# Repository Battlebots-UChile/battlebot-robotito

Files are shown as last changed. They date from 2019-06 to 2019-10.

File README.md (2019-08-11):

# Robotito
Robotito fue realizado en el taller de proyecto "Contruye tu battlebot", el cuál combina conocimientos de electrónica, mecánica y programación, bajo un acorazado de metal giratorio.
<center><center>

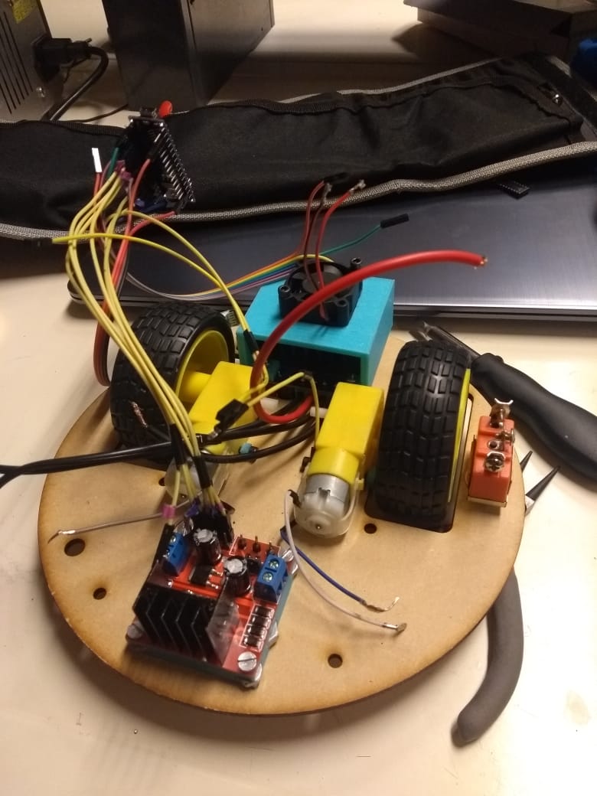
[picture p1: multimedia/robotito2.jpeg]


## Integrantes
- Leslie Cárdenas - FCFM
- Tomás Ceballos - FCFM
- Francisca Guiñez - FCFM
- Keyla Sandoval - FCFM

## Descripción del proyecto

Robotito es un robot, pero no cualquier tipo de robot, NOOO... es un BATTLEBOT (por si no quedo claro en los títulos), controlado mediante una aplicación celular (App-Inventor), cuyo objetivo en la vida es detener todos los golpes que intenten destruirlo.

Funciona en base a dos motores DC básicos, uno conectado a cada rueda, y un motor DC de 2500 rpm conectado a un bowl de cocina, a través de una pieza impresa en 3D. Cuenta con dos puentes H, uno dual y uno single, y es alimentado por dos baterias LiPo.

### Descripción morfológica
La forma elegida para nuestro robot surgió de pensar en cual sería la más óptima defensiva. Por esto nos inclinamos por utilizar un bowl. Pensamos que, por un lado, su forma semiesférica iba a imposibilitar cualquier intento de agarrarlo.
Además, al estar hecho de acero inoxidable claramente iba a ser poco probable que le produjeran daños graves.

Cabe decir que antes de tomar una decisión realizamos una exhaustiva investigación en Youtube sobre battlebots alrededor del mundo

### Estrategia utilizada

La mejor estrategia para ganar con Robotito es:
- Evitando ataques laterales: Creemos que lo que podría dañar el bowl serían golpes muy reiterativos, contundentes y punzantes de alguna forma. Por ejemplo una barra o punta de un material lo suficientemente resistente. Por lo que lo ideal es evitarlos.
- Interponiendosea a la trayetoria del arma del robocontrincante: Como Robotito es un bowl de metal, en general los golpes no lo afectan. La idea es entonces que el motor que controla el arma del contrincante sea sometido a pick de corriente que lo imposibiliten de seguir golpeandolo por un tiempo. Esto para dar opcion al siguiente punto.
- Alejarse del oponente cuando sea posible: Esto es mas que todo para evitar golpes innecesarios que no vayan a ayudar en la estrategia anteriormente mencionada. Es una buena idea alejarse, luego posicionarse y direccionarse hacia el roboenemigo en busca de un empujón que lo lleve al borde la pista, o bien, hacia alguna arma que pueda haber en esta.  
Una demostración de esto se puede ver [aquí](https://drive.google.com/file/d/1hvNaAUOcBa2c_J4brZBd_sA4WgRW3LiS/view?usp=sharing).

#### Datos defensivos
El bowl es nuestra principal , pero no única, defensa. Es de acero inoxidable. Proviene directamente de la cocina de una de las integrantes de nuestro grupo :).  
Pero como un pedazo de metal no puede con todo (¿o si?), para detener los posibles ataques a ras de suelo (ya que el bowl deja un par de centímetros al descubierto), nuestro battlebot cuenta con lo que denominamos una "falda", cortada con laser en MDF de 6mm.
Además, cabe decir que la forma circular o semiesférica conseguida también ayuda a que los golpes no lleguen de forma directa.

### Descripción control
Robotito tiene su propia app para Android, la cual pueden descargar [aquí](https://github.com/Battlebots-UChile/battlebot-robotito/tree/master/codigos/APK).
Al ingresar, se pueden ver 3 secciones:

#### Conexión
Para conectar la app al módulo BT del robot, basta con:
1. Prender el robot (nunca está de más cerciorarse)
2. Activar el Bluetooth del celular
3. Entrar a la app desde el celular
4. Presionar "Buscar dispositivos"
5. Seleccionar el nombre correspondiente al módulo bluetooth (modificable, Google es la luz)
6. Esperar. Cuando la luz del módulo BT deje de parpadear, será un indicador de que se ha establecido una conexión.

#### Movimiento
Estos 7 botones cumplen con el objetivo de movilizar nuestro robot. Cuando se presiona un botón, la orden se manda de manera constante, es decir, que, a menos que se presione otro, la acción se seguirá ejecutando.  
A continuación, se especifica cómo giran los motores, dependiendo del botón presionado. 
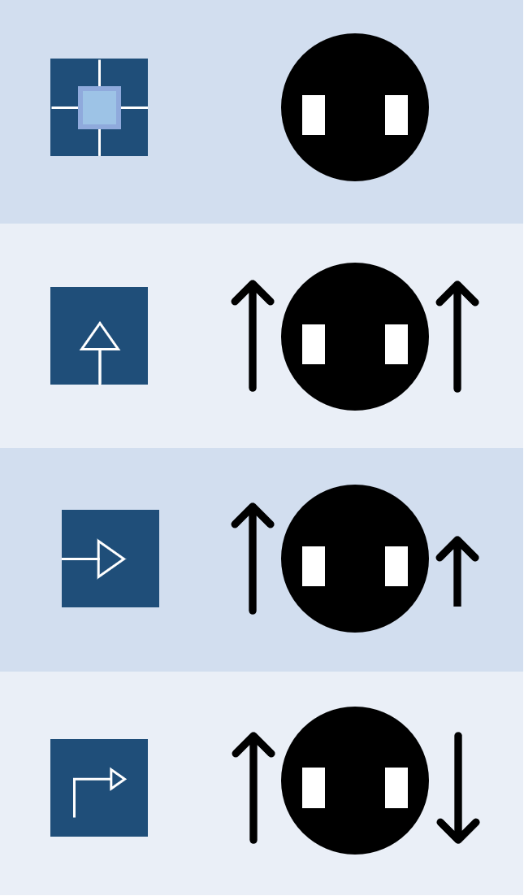
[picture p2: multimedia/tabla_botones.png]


#### Arma y emergencia
En caso de emergencia de debe presionar el botón STOP. ¿Qué hace? Manda una señal que detiene el movimiento de los 3 motores que componen a Robotito de manera instantánea (en cuando la señal sea recibida). No afecta el funcionamiento del ventilador, ya que funciona de manera independiente.
Luego, podemos ver una numeración de 5 botones, los cuales son las posibles velocidades del arma (se pueden modificar dentro del código. ino, pero no lo sugerimos). En "0" el motor no se mueve. Si se presiona cualquiera que modifique la velocidad actual, el aumento o descenso será paulatino.
#### Otros
La app también cuenta con un particular sonido al presionar algunas de las teclas. Fuente: desconocida.  
Además, cuenta con la posibilidad de activar la reproducción de la canción "Mr. Roboto", presionando el switch de la parte inferior.

##  Paso a Paso

### Materiales:
- 1 Arduino Nano
- 1 Bowl de acero inoxidable
- 1 Rueda loca
- 2 Motores DC con ruedas
- 1 Puente H BTS7960
- 1 Puente H dual L298n
- 1 Módulo Bluetooth HC-06
- 2 Baterías Li-Po de 7.4V
- 1 Ventilador de 30x30mm
- 3 Ruedas de 20mm
- 4 Separadores hexagonales de 50mm (\*)
- 20 cm de Velcro
- 2 Conectores hembra HT60 (\*\*)
- 2 Interruptores (\*\*\*)
- 4 Pernos de 2mm
- 2 Tuercas de 2mm
- Pernos y tuercas de 3mm
- Cables
- Cables para Arduino
- Placa MDF de 3mm (opcional 6mm)
- Soldadura para electrónica
- Termoretráctil de varias medidas
- Adhesivo instantáneo, como La Gotita (\*\*\*\*)
- Pines hembra

### Herramientas:
- Alicates varios
- Destornilladores varios
- Pistola de calor o encendedor
- Cautín
- Dremel
- Impresora 3D
- Cortadora Láser
- Limas metálicas
- Pistola de silicona c/repuestos
- Celular Android

### Opcionales:
- Alarma para Li-Po
- Cargador de Li-Po

(\*) o alguna combinación que resulte en esa altura.  
(\*\*) o del tipo que corresponda, según el conector de las LiPos.  
(\*\*\*) Debe poder soportar la corriente del motor. Nosotros usamos uno que soportaba 15A.  
(\*\*\*\*) No nos auspician :(
### Instrucciones

1. Imprimir las piezas en 3d, desde [aquí](https://github.com/Battlebots-UChile/battlebot-robotito/tree/master/planos/Piezas%203d), según lo que se indica en su descripción, y lijar para eliminar imperfecciones.  
2. Cortar las dos bases para el robot, desde [aquí](https://github.com/Battlebots-UChile/battlebot-robotito/tree/master/planos/Bases) y quitar imperfecciones.
3. Conectar el Arduino Nano a un PC, y cargar el [codigo](https://github.com/Battlebots-UChile/battlebot-robotito/tree/master/codigos/arduino/app_bt).
4. Descargar el [apk](https://github.com/Battlebots-UChile/battlebot-robotito/tree/master/codigos/APK) mediante el celular y ejecutar el instalador.
5. Probar las componentes individualmente.
6. Ubicar los [motores DC](https://www.wiltronics.com.au/wp-content/uploads/images/make-and-create/gear-motor-dc-toy-car-wheel-arduino.jpg) con sus respectivas ruedas, utilizando el [agarre 1](https://github.com/Battlebots-UChile/battlebot-robotito/blob/master/planos/Piezas%203d/agarre_yellowmotor1.stl) y el [agarre 2](https://github.com/Battlebots-UChile/battlebot-robotito/blob/master/planos/Piezas%203d/agarre_yellowmotor2.stl) en la base cortada con láser que tiene los orificios para las ruedas, utilizando 4 pernos de 3mm. Esta parte puede ser un poco complicada, pero de ser necesario las piezas 3d se pueden lijar un poco más.   
Para reforzar, aplicar el adhesivo instantáneo a la unión entre las piezas 3d y la base. 
7. Solo con pernos(3mm) (con 2 es suficiente), agarrar el ventilador a la [base del ventilador](https://github.com/Battlebots-UChile/battlebot-robotito/blob/master/planos/Piezas%203d/base_ventilador.stl) y posteriormente al puente H BTS7960. Esto último, solo con 2 orificios opuestos utilizando pernos de 2 mm (la tuerca va puesta por el lado de la pieza 3d).
8. A la estructura anterior, agregarle la [base](https://github.com/Battlebots-UChile/battlebot-robotito/blob/master/planos/Piezas%203d/base_bts7960.stl), utilizando pernos de 3 mm, y ensamblar a la base de las ruedas en la posición determinada. En este punto se puede notar que los pines del puente H quedan hacia la base. Nosotros creamos una pequeña pieza, que no ha sido detallada, debido a que tuvo fallas y será definitivamente modificada.
9. Juntar el puente H L298n a su respectiva [base](https://github.com/Battlebots-UChile/battlebot-robotito/blob/master/planos/Piezas%203d/base_l298n.stl). Para esto, primero se deben ubicar las tuercas en los orificios que correspondan. Luego, con pernos de un largo limitado (posiblemente deban cortarlos), agarrar el puente H.
10. Ensamblar como se detalla en el [esquema](https://github.com/Battlebots-UChile/battlebot-robotito/blob/master/multimedia/esquema_rueda.png), agregando pernos donde corresponda.
11. Cortar dos pedazos de velcro, del tamaño de las baterías y, con silicona caliente (y mucho cuidado, nunca se sabe), pegárselos.
12. Para fijar el Arduino a la base de arriba, también se hizo una pieza, que se evidencia en la siguiente imagen. (algún día estará acá)
13. Agregar los interruptores en los orificios laterales a las ruedas.
14. Usar [esto](https://github.com/Battlebots-UChile/battlebot-robotito/blob/master/planos/Piezas%203d/agarre_motorarma.stl) para fijar el motor del arma a la base de arriba. Primero introducir con mucho cuidado los pernos que agarran el motor con la pieza 3d.
15. Teniendo en cuenta las [conexiones](https://github.com/Battlebots-UChile/battlebot-robotito/tree/master/diagrama), ahora se puede comenzar a cablear.  
Tener en cuenta: no mantener conectadas las baterías cuando se realice esto. Tener claro cuando los interruptores no están dejando pasar energía. Todas los GND deben estar conectados. La base de arriba tiene orificios para los conectores HT60 de las baterías. Para las conexiones desde la LiPo al puente H BTS7960 se debe utilizar un cable más grueso que pueda soportar altos de corriente.
16. Probar las direcciones de las ruedas, si estas no tienen sentido, probar rotar cables de los motores de las ruedas.
17. Si existe algún otro problema operacional, consultar sección [Problema-Solución](https://github.com/Battlebots-UChile/battlebot-robotito#problema---solución)
18. Una vez que todos los motores funcionen según las indicaciones dadas por la app, se recomienda fijar los cables de Arduino con silicona caliente, o en el caso de ser necesario, soldar.
19. Agregar los separadores en los espacios determinados con pernos y tuercas.
20. Al bowl realizarle 3 orificios con un taladro a 40mm desde el centro, ser lo más preciso posible. Esto puede ser muy complicado, por lo que: paciencia.
21. Fijar la [pieza](https://github.com/Battlebots-UChile/battlebot-robotito/blob/master/planos/Piezas%203d/agarre_motorbowl.stl) al bowl, usando pernos.
22. Posicionar la pieza anterior sobre el motor del arma.
23. Destruir a todos

## Problema - Solución
1. Conexiones sueltas  	
Inicialmente teníamos muchas conexiones que estaban agarradas mediante cinta aislante. Pero llegó un punto en el desarrollo del robot donde esto no era eficiente, ya que, debido a la gran cantidad de cables y componentes, estas se soltaban regularmente y entorpecía el avance.  
Solución: Aprender a soldar. Soldar todo lo que estaba más o menos fijo (referido a: Si, este cable va con este hasta el fin de los tiempos) y obviamente funcional.

2. No se cargaba el código al Arduino  
El principal error cuando uno se inicia en el uso de Arduino y módulos BT, es conectar los pines RX y TX con sus opuestos en el otro dispositivo. En el Arduino estos están designados a los pines 0 y 1, pero cuando están ocupados: no se le puede cargar otro código, ni tampoco interactuar con el Serial.  
Solución: Designar nuevos pines RX y TX dentro del Arduino, con la librería SofwareSerial. 

3. El motor del arma no giraba de manera constante  
Desde un principio, la corriente del motor del arma fue desconocida, por lo que, al momento de conectarlo a diversas pilas y baterías, no alcanza la velocidad ni la fuerza que buscábamos.  
Solución: Utilizar baterías LiPo. Su principal característica es que puede entregar mucha corriente en poco tiempo, justo lo que necesitábamos.

4. Quemamos un puente H  
La gran cantidad de amperaje quemo nuestro puente H inicial (VNH2SP30), ya que los 30A que supusimos podía soportar eran solo para picks, no de manera continua. Por esto, se calentaba hasta los 70-100°C.  
Solución: Lo reemplazamos por el BTS7960, capaz de soportar 40A de manera continua. Este cuenta un disipador bastante grande y un ventilador.

5. Cables rozando con el bowl  
Provocaba que el motor del arma necesitara más corriente para funcionar y ocasionaba que las baterías se gastaran más rapido.  
Solución: Tomar los cables del piso superior con una pieza plástica y pegar otros con silicona caliente.

6. Falta de espacio  
Al decidirnos a utilizar un bowl, creímos que el espacio no iba a ser un problema, pero con el cambio de baterías, nos faltaba.  
Solución: Cambiar un Arduino Uno por un Arduino Nano. Reubicar componentes.

### Proyecciones a futuro
* Cambiar el método de control: es decir, en vez de usar la App, crearemos un control con botones y un joystick. Esto ya está en proceso y sus respectivos códigos están actualizados y funcionales.
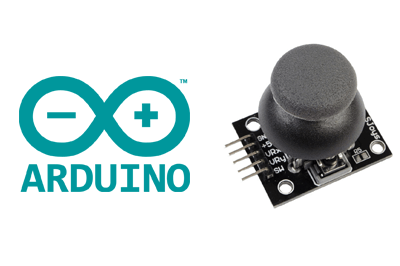
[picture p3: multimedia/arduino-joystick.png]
Joystick con Arduino
#### 
* Adición de un arma: Fijaremos a la parte inferior del bowl una estructura hecha de placa MDF, la cual constará de un anillo con tres protuberancias. La idea es que debido a la velocidad y la fuerza con la que gira el bowl, si un roboenemigo se acerca lo suficiente, este sera levantado y dejado caer en reiteradas ocasiones en un periodo corto de tiempo, con la intención de provocar sacudidas que puedan dañar interna y/o externamente a los demás robots. (Planos: Próximamente...)

## Licencia
<br />Esta obra está bajo una <a rel="license" href="http://creativecommons.org/licenses/by-nc/4.0/">Licencia Creative Commons Atribución-NoComercial 4.0 Internacional</a>.

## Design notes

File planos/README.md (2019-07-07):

# Archivos de planos incluidos

 En esta carpeta se encuentran todos los planos pra la cortadora laser o la impresora 3D, las dos sub-carpetas son:

 - Bases: en ella  esta contenida la estrucutura interna del battlebot construida con placa MDF de 6mm en una cortadora láser
 - Piezas 3D: Aquí estan todas las estructuras hechas en impresora 3D , las cuales son principalmente de agarre a la estrucutura principal del battlebot y al bool

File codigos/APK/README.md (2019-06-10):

# Código de la Aplicación
Este aplicacion fue usada en la primera version de Robotito.

Cuenta con botones para controlar la velocidad del arma principal y la dirección del robot.

Subir archivo **.apk** y código de la APK ([descargar desde acá](http://appinventor.mit.edu/explore/support/sharing-code.html))

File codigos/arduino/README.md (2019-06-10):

# Códigos Arduino

Robotito_bluetooth cuanta con el código necesario para controlar al robot, mediante la app.

(En proceso) 
Robotito_joystick cuenta con los códigos necesarios para controlar al robot, mediante el Control.
control.ino va cargado al arduino del control
robot.ino va cargado al arduino del robot

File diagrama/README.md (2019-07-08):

# Diagrama electromecánico
 Aquí se encuentran los digramas eléctricos de robotito en tres formatos, dos visuales y uno en extension fzz.
 Los archivos con extensión jpg muestran todos los componentes y sus conexiones siendo uno hecho en fritzing por lo que el lenguaje y simbología del mismo es un poco más compleja y profesional; el otro archivo es de thinkercad por lo que visualemte es más comprensible, es recomendado empezar por este.

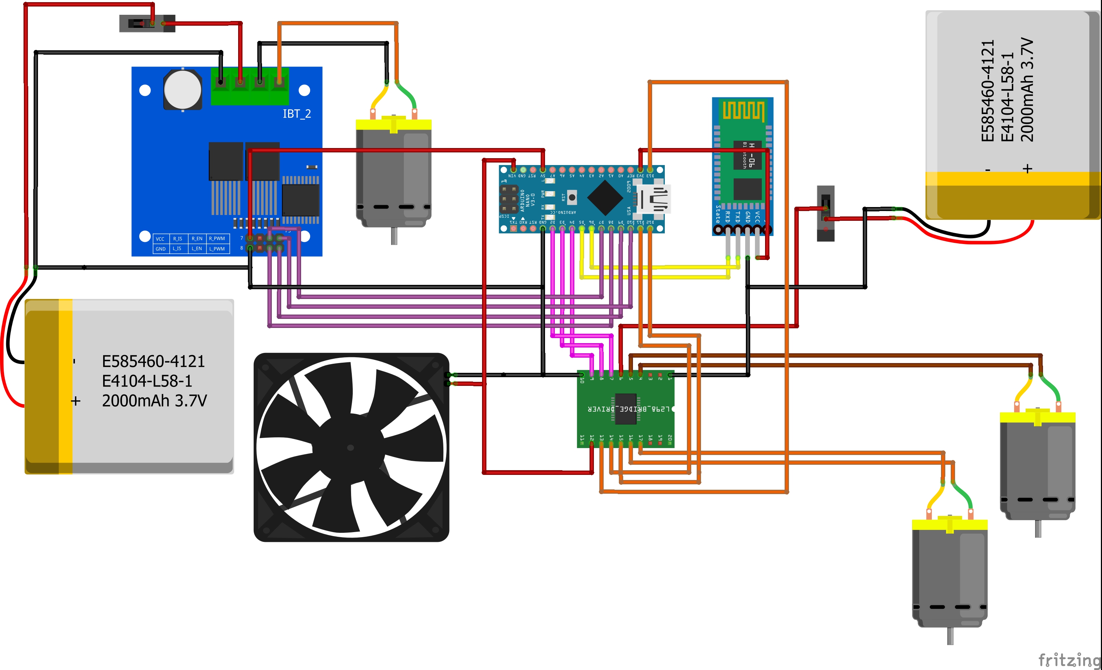
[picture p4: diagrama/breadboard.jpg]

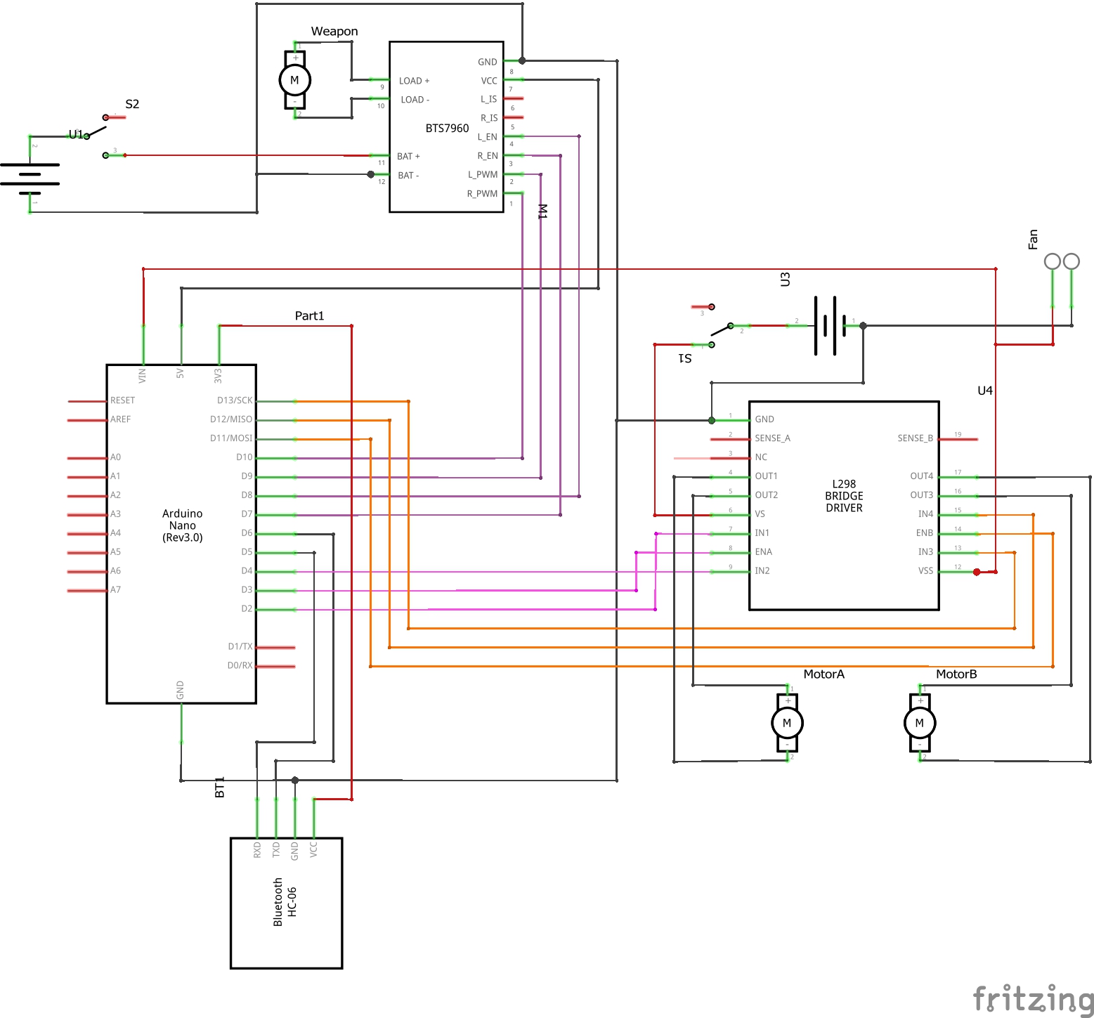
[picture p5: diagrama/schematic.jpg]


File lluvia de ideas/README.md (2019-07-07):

# Lluvia de Ideas
Iniciamos nuestro proyecto solo con dos opciones :Una constaba de un carro convencional con la  particuliaridad de una plataforma movible cuya función era ubicarse bajo los otros robots y mediante un mecanismo levantarlos volcándolos lo que nos haría ganar la batalla. El segundo modelo  (que fue el elegido) era una especie de platillo volador (inspirado en el mismo concepto) con ruedas pero que podía girar sobre si mismo.
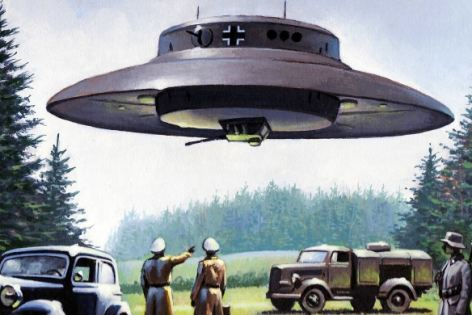
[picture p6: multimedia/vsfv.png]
Modelo 2(OVNI)
#### 

Las armas eran variadas pero se centraba en:Un paralelepípedo giratorio con puntas en los bordes acoplado en el “techo” del OVNI o carro.
Una bola metálica acoplada a una varilla giratoria pegada en el techo del OVNI o carro(todavía no se sabía si era una cuerda o directamente una varilla rigida)
#### Bosquejos con armas integradas
En esta imagen se ven ambos prototipos con las armas anteriormente mencionadas en especial con la bola de demolición.El primero es el OVNI con la bola e inclusive en su momento barajamos la opcion de poner mas de una que solo se movieran con el casco; el segundo bosquejo es el carro tambien con la bola.

Estas dos vías entre battlebots respondían a dos necesidades, proteccion y ataque; la opción de la plataforma brindaba una especie de "falda" que evitaria que otros robots se metieran por debajo con sus armas y nos volcaran o sacaran nuestra tripas. El segundo modelo dada a la velocidad del giro evitaría que fuesemos golpeados directamente y en realidad ver este modelo en acción a travéz de battlebot GIGABYTE  en la pelea  (https://www.youtube.com/watch?v=hSRnhd6K6kY) nos convencio para seguir ese camino.
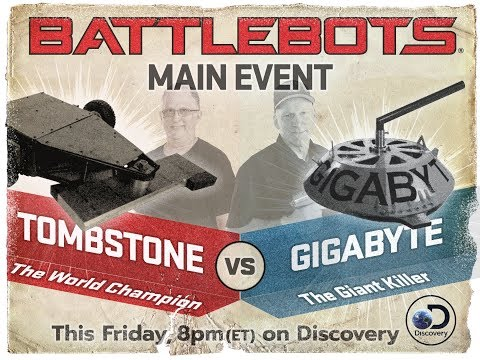
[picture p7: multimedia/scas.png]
Pariente de robotito
####

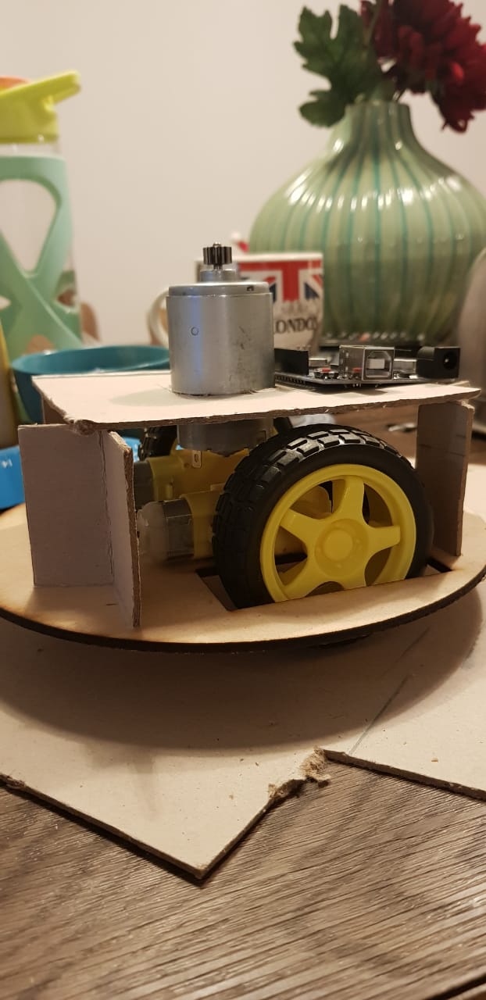
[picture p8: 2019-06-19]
multimedia/cuerpo.jpeg

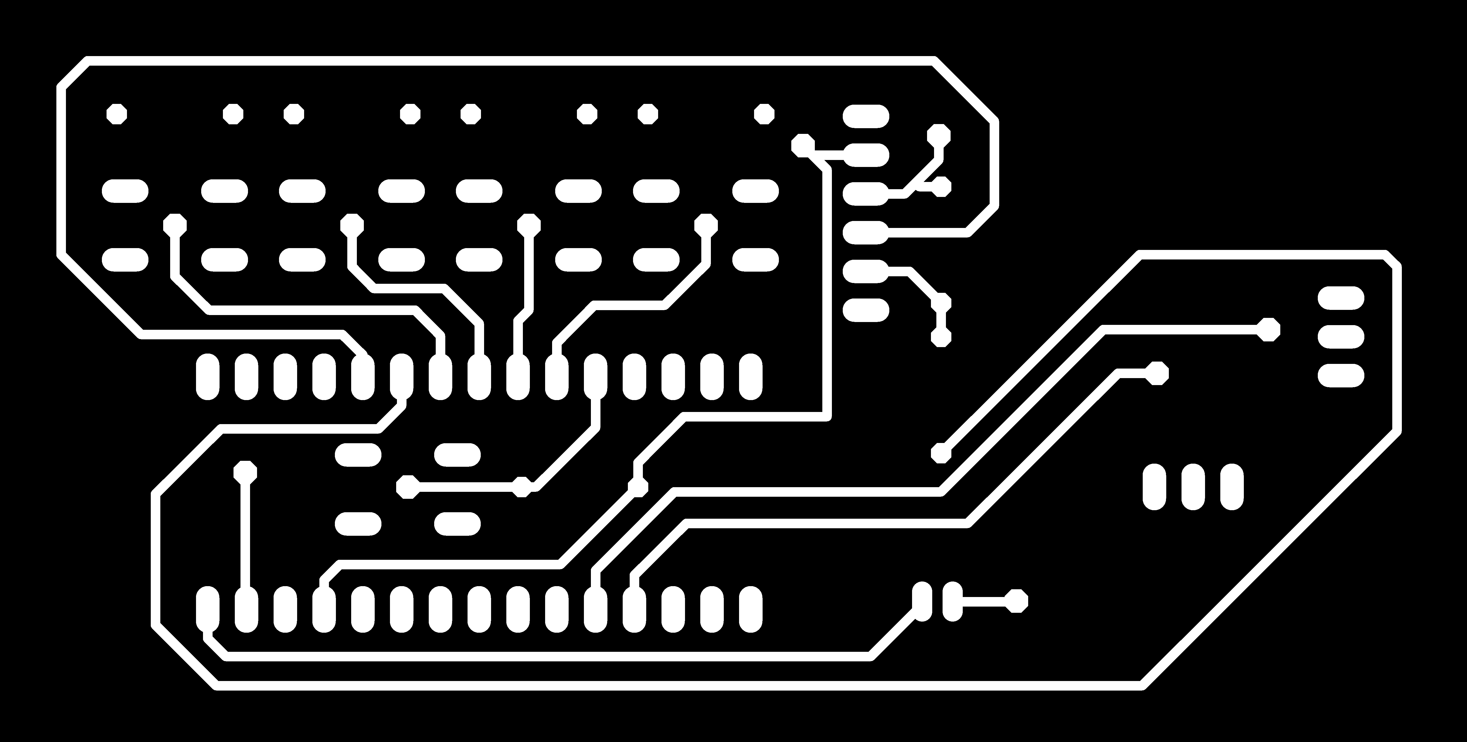
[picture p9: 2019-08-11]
planos/PCB/top.png

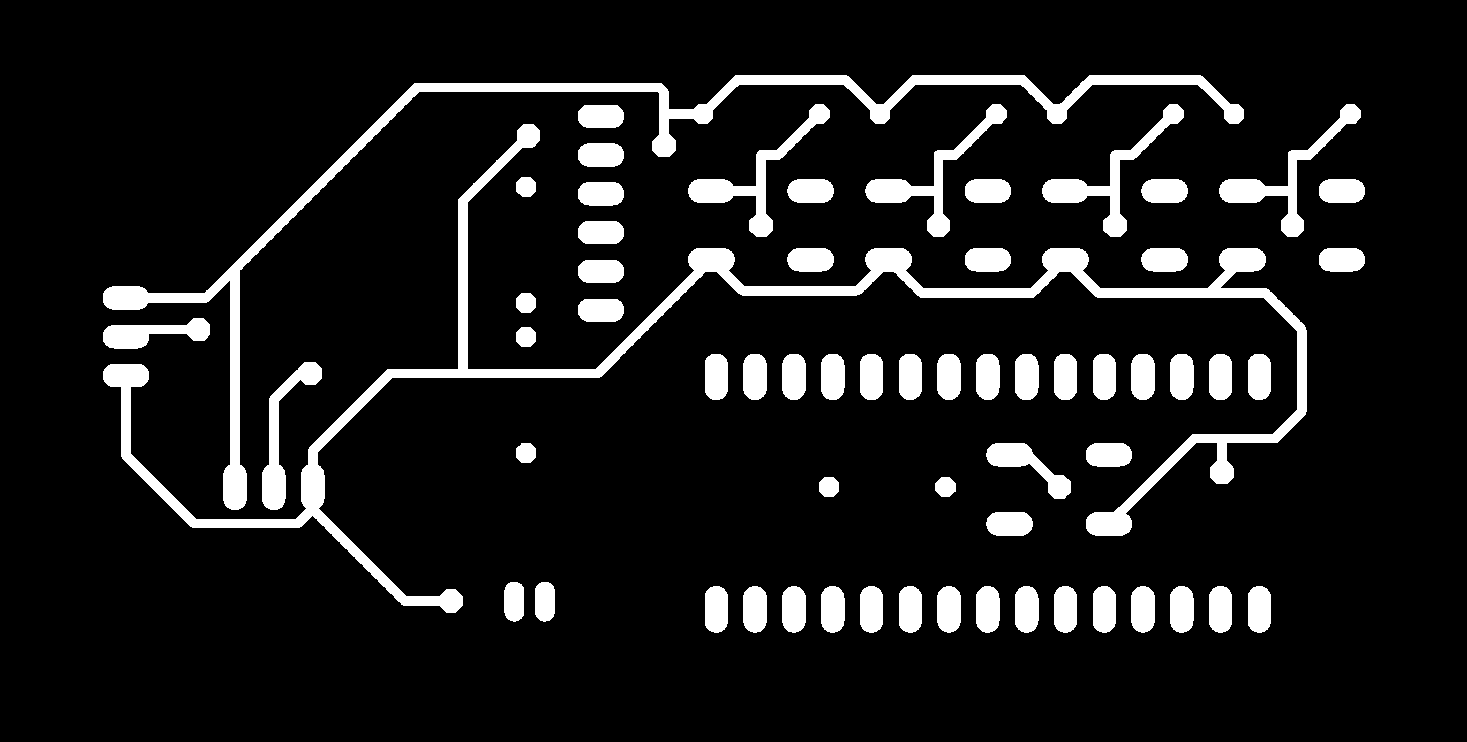
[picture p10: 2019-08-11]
planos/PCB/bottom.png

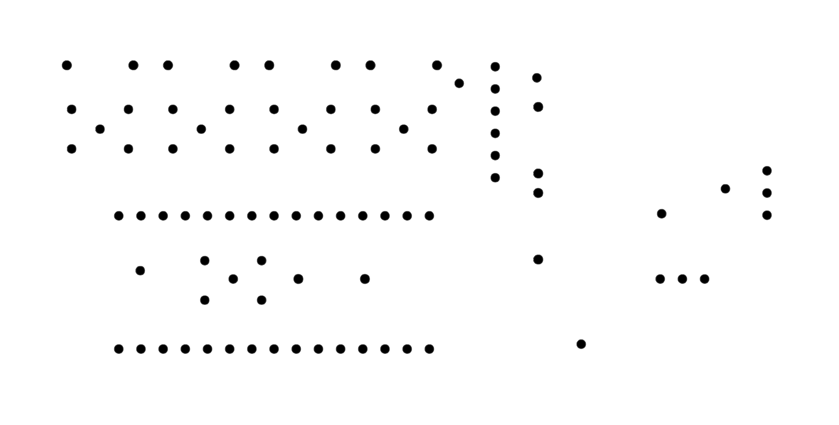
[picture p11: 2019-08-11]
planos/PCB/drills.png

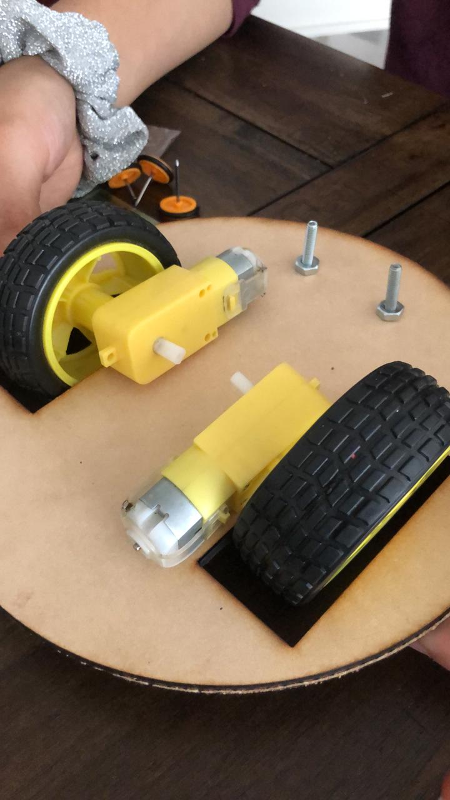
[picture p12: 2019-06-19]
multimedia/ruedas.jpeg

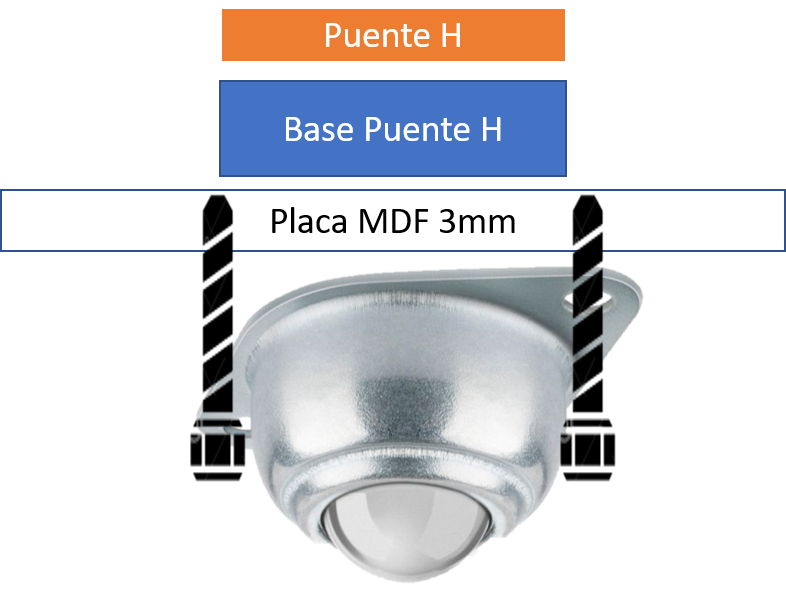
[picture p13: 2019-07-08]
multimedia/esquema_rueda.png

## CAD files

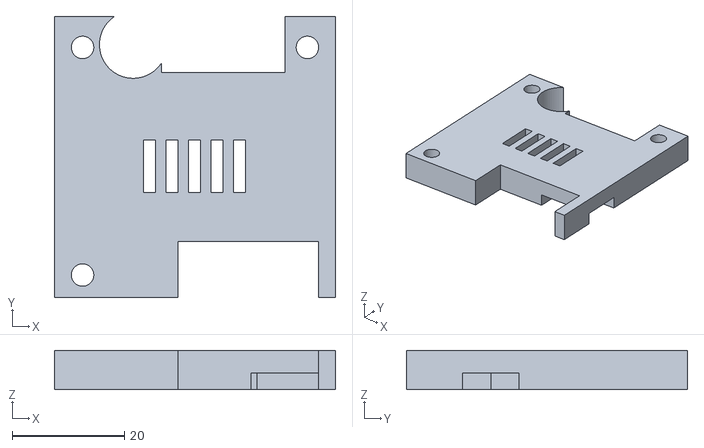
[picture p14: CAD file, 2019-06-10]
planos/Piezas 3d/base_bts7960.stl
50.0 x 50.0 x 7.00

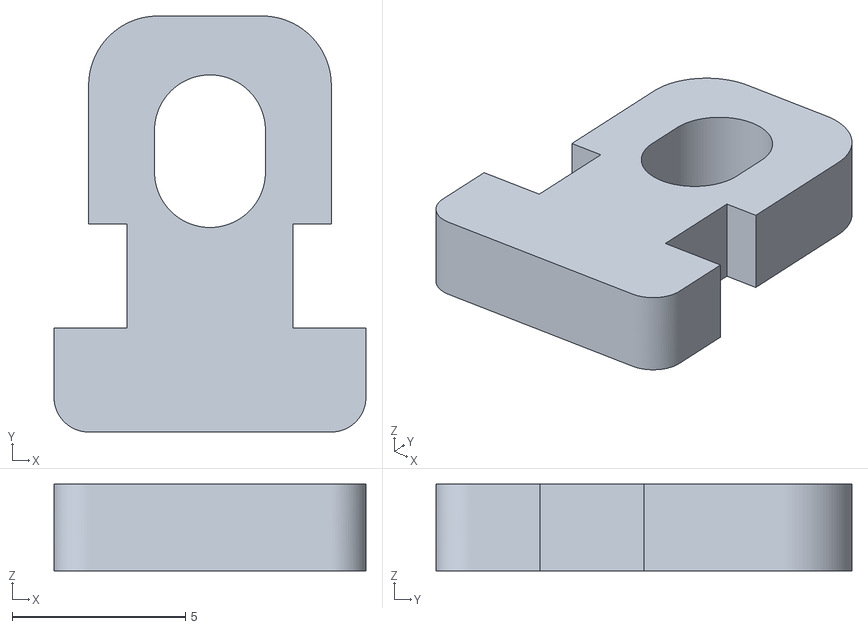
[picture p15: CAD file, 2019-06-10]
planos/Piezas 3d/agarre_yellowmotor1.stl
9.00 x 12.0 x 2.50

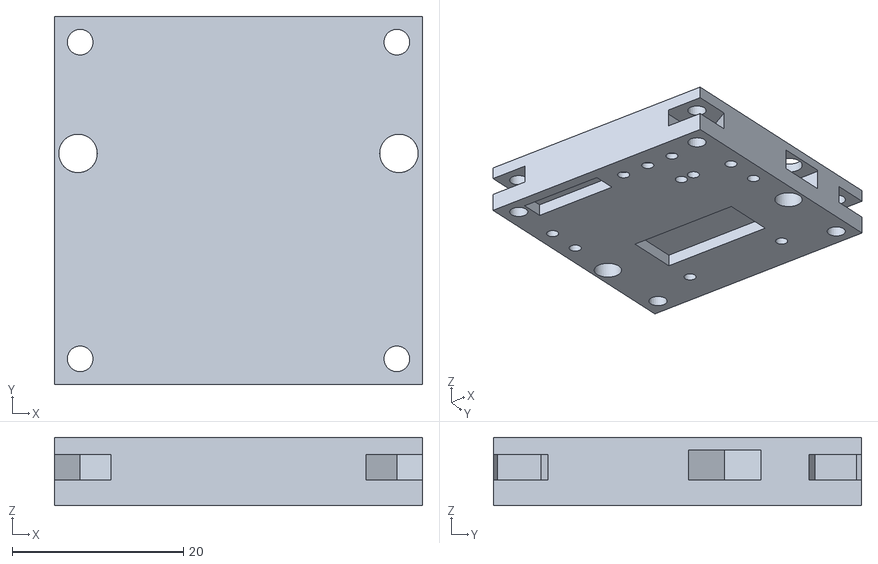
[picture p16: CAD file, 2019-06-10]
planos/Piezas 3d/base_l298n.stl
43.0 x 43.0 x 8.00

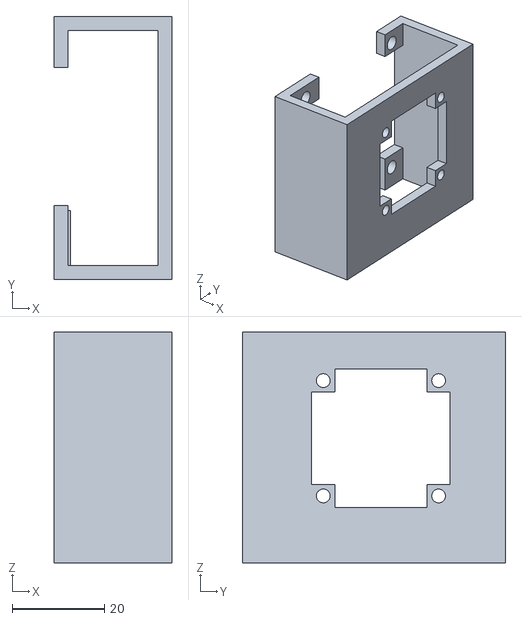
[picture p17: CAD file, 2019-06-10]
planos/Piezas 3d/base_ventilador.stl
25.5 x 57.0 x 50.0

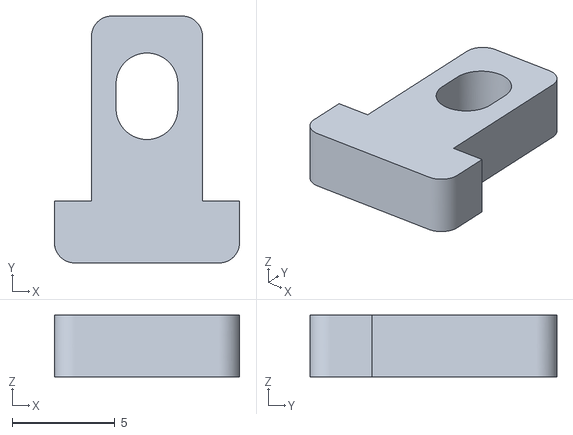
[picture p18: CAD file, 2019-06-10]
planos/Piezas 3d/agarre_yellowmotor2.stl
9.00 x 12.0 x 3.00

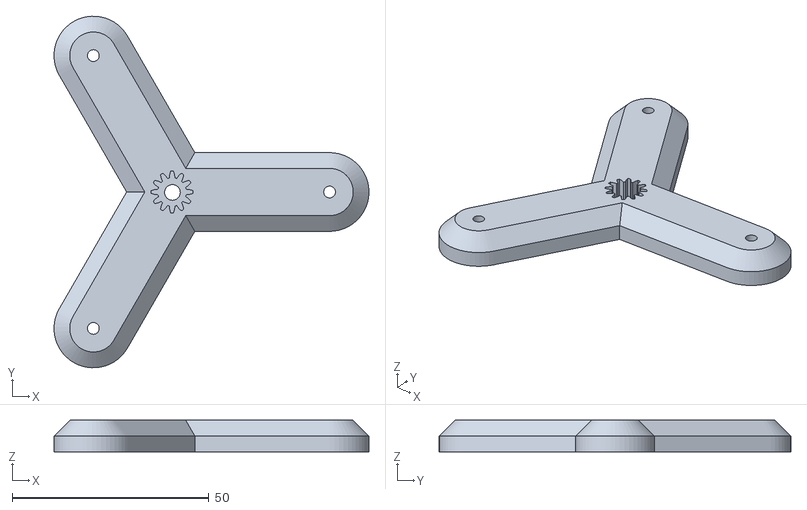
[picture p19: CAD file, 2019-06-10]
planos/Piezas 3d/agarre_motorbowl.stl
80.0 x 89.3 x 8.00

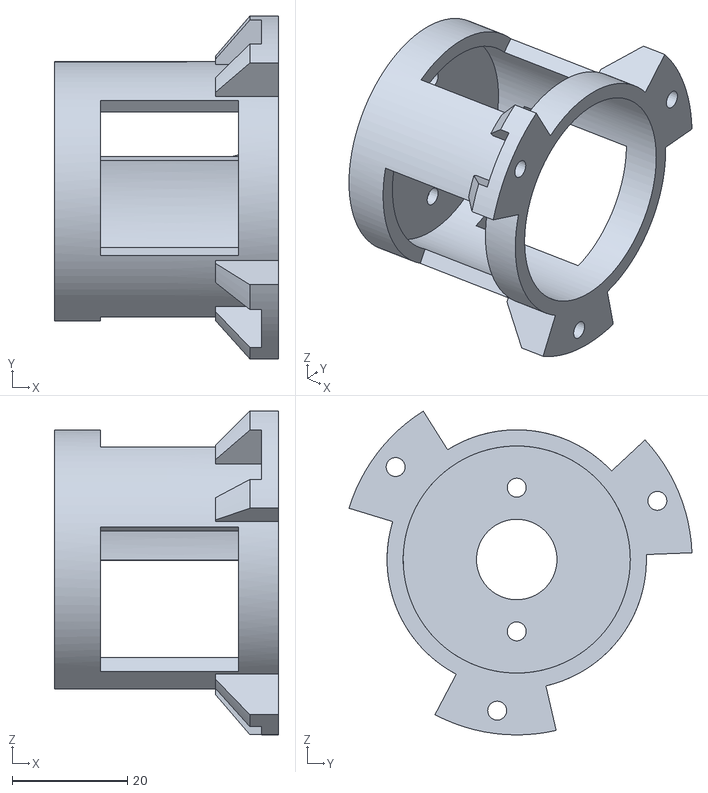
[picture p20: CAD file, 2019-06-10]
planos/Piezas 3d/agarre_motorarma.stl
39.0 x 59.6 x 56.3

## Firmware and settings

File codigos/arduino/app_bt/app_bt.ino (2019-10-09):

//version del codigo para controlar a Robotito mediante la aplicación

//no se está usando, puede llegar a ser útil
enum Estado {
  VEL_FIJA,
  VEL_VAR,
};

int estado_arma = Estado::VEL_FIJA;

int state;

int motorA_vel = 0;
int motorB_vel = 0;

int vel_actual = 0;
int vel_nueva = 0;
int vel_salto = 2;

//nuevos pines RX y TX
#include <SoftwareSerial.h>
SoftwareSerial SerialBT(5, 6);

//bluetooth
#define PIN_BT_TX 5
#define PIN_BT_RX 6

// motor A, izquierdo
#define PIN_MOT_A1 2    //IN1
#define PIN_MOT_A2 4    //IN2
#define PIN_MOT_AEN 3   //ENA

//motor B, derecho
#define PIN_MOT_B1 13    //IN3
#define PIN_MOT_B2 12    //IN4
#define PIN_MOT_BEN 11   //ENB

//motor arma
#define PIN_ARMA_PWMR 10
#define PIN_ARMA_PWML 9
#define PIN_ARMA_ENR 7
#define PIN_ARMA_ENL 8

void setup() {

  configurarBluetooth();
  configurarMotoresMovimiento();
  configurarArma();

  Serial.begin(9600);
  //SerialBT.begin(9600);
}

void loop() {
  
  digitalWrite(PIN_MOT_A1, LOW);
  digitalWrite(PIN_MOT_A2, HIGH);
  digitalWrite(PIN_MOT_B1, HIGH);
  digitalWrite(PIN_MOT_B2, LOW);
  motorA_vel = 255;
  motorB_vel = 255;
  analogWrite(PIN_MOT_AEN, motorA_vel);
  analogWrite(PIN_MOT_BEN, motorB_vel);
  delay(1000);
  motorA_vel = 100;
  motorB_vel = 100;
  analogWrite(PIN_MOT_AEN, motorA_vel);
  analogWrite(PIN_MOT_BEN, motorB_vel);
  delay(1000);

  // Chequear Serial
  //leerSerial();

  //Detener todo
  //detenertodo();

  // Mover el robot
  //moverRobot();

  // Mover el arma
  //setVelArma();

}

void setVelArma() {
  if (state == 'G') {
    vel_nueva = 0;
  }
  else if (state == 'H') {
    vel_nueva = 75;
  }
  else if (state == 'J') {
    vel_nueva = 100;
  }
  else if (state == 'K') {
    vel_nueva = 150;
  }
  else if (state == 'L') {
    vel_nueva = 200;
  }
  check_vel();

}

void check_vel() {
  if (vel_actual > vel_nueva) {
    disminuir_vel();
  }
  else if (vel_actual < vel_nueva) {
    aumentar_vel();
  }
}

void disminuir_vel() {
  vel_actual -= vel_salto;
  analogWrite(PIN_ARMA_PWML, vel_actual);
  delay(25);
}

void aumentar_vel() {
  vel_actual += vel_salto;
  analogWrite(PIN_ARMA_PWML, vel_actual);
  delay(25);
}

void moverRobot() {
  //direcciones
  if (state == 'E') {
    rotarRobot_izquierda();
  }
  else if (state == 'Q') {
    rotarRobot_derecha();
  }
  else if (state == 'S') {
    moverRobot_atras();
  }
  else if (state == 'W') {
    moverRobot_adelante();
  }
  else if (state == 'A') {
    moverRobot_derecha();
  }
  else if (state == 'D') {
    moverRobot_izquierda();
  }
  else if (state == 'P') {
    pararRobot();
  }
}

void detenertodo() {
  if (state == 'M') {
    pararRobot();
    digitalWrite(PIN_MOT_AEN, LOW);
    digitalWrite(PIN_MOT_BEN, LOW);
    analogWrite(PIN_ARMA_PWML, 0);
    analogWrite(PIN_ARMA_PWMR, 0);
  }
}

void leerSerial() {
  SerialBT.listen();
  if (SerialBT.available() > 0) {
    state = SerialBT.read();
  }
}

void moverRobot_derecha() {
  // mover a la derecha

  motorA_vel = 255;
  motorB_vel = 150;
  analogWrite(PIN_MOT_AEN, motorA_vel);
  analogWrite(PIN_MOT_BEN, motorB_vel);

  digitalWrite(PIN_MOT_A1, LOW);
  digitalWrite(PIN_MOT_A2, HIGH);
  digitalWrite(PIN_MOT_B1, HIGH);
  digitalWrite(PIN_MOT_B2, LOW);
}
void moverRobot_izquierda() {
  // mover a la izquierda

  motorA_vel = 150;
  motorB_vel = 255;
  analogWrite(PIN_MOT_AEN, motorA_vel);
  analogWrite(PIN_MOT_BEN, motorB_vel);

  digitalWrite(PIN_MOT_A1, LOW);
  digitalWrite(PIN_MOT_A2, HIGH);
  digitalWrite(PIN_MOT_B1, HIGH);
  digitalWrite(PIN_MOT_B2, LOW);
}
void moverRobot_atras() {
  // mover hacia atras

  motorA_vel = 255;
  motorB_vel = 255;
  analogWrite(PIN_MOT_AEN, motorA_vel);
  analogWrite(PIN_MOT_BEN, motorB_vel);

  digitalWrite(PIN_MOT_A1, HIGH);
  digitalWrite(PIN_MOT_A2, LOW);

  digitalWrite(PIN_MOT_B1, LOW);
  digitalWrite(PIN_MOT_B2, HIGH);
}
void moverRobot_adelante() {
  // mover hacia adelante

  motorA_vel = 255;
  motorB_vel = 255;
  analogWrite(PIN_MOT_AEN, motorA_vel);
  analogWrite(PIN_MOT_BEN, motorB_vel);

  digitalWrite(PIN_MOT_A1, LOW);
  digitalWrite(PIN_MOT_A2, HIGH);
  digitalWrite(PIN_MOT_B1, HIGH);
  digitalWrite(PIN_MOT_B2, LOW);
}

void rotarRobot_derecha() {
  // rotar a la derecha

  motorA_vel = 200;
  motorB_vel = 200;
  analogWrite(PIN_MOT_AEN, motorA_vel);
  analogWrite(PIN_MOT_BEN, motorB_vel);

  digitalWrite(PIN_MOT_A1, LOW);
  digitalWrite(PIN_MOT_A2, HIGH);
  digitalWrite(PIN_MOT_B1, LOW);
  digitalWrite(PIN_MOT_B2, HIGH);
}

void rotarRobot_izquierda() {
  // rotar a la izquierda

  motorA_vel = 200;
  motorB_vel = 200;
  analogWrite(PIN_MOT_AEN, motorA_vel);
  analogWrite(PIN_MOT_BEN, motorB_vel);

  digitalWrite(PIN_MOT_A1, HIGH);
  digitalWrite(PIN_MOT_A2, LOW);
  digitalWrite(PIN_MOT_B1, HIGH);
  digitalWrite(PIN_MOT_B2, LOW);
}

void pararRobot() {

  //detener motores
  digitalWrite(PIN_MOT_A1, LOW);
  digitalWrite(PIN_MOT_A2, LOW);
  digitalWrite(PIN_MOT_B1, LOW);
  digitalWrite(PIN_MOT_B2, LOW);
}

void configurarBluetooth() {

  //Pines Bluetooth
  pinMode(PIN_BT_TX, INPUT);
  pinMode(PIN_BT_RX, INPUT);
}

void configurarMotoresMovimiento() {

  //Pines Motor A
  pinMode(PIN_MOT_A1, OUTPUT);
  pinMode(PIN_MOT_A2, OUTPUT);
  pinMode(PIN_MOT_AEN, OUTPUT);
  digitalWrite(PIN_MOT_AEN, HIGH);

  //Pines Motor B
  pinMode(PIN_MOT_B1, OUTPUT);
  pinMode(PIN_MOT_B2, OUTPUT);
  pinMode(PIN_MOT_BEN, OUTPUT);
  digitalWrite(PIN_MOT_BEN, HIGH);
}

void configurarArma() {

  //Pines Motor Arma
  pinMode(PIN_ARMA_PWMR, OUTPUT);
  pinMode(PIN_ARMA_PWML, OUTPUT);
  pinMode(PIN_ARMA_ENR, OUTPUT);
  pinMode(PIN_ARMA_ENL, OUTPUT);

  digitalWrite(PIN_ARMA_PWMR, LOW);
  digitalWrite(PIN_ARMA_PWML, LOW);
  digitalWrite(PIN_ARMA_ENR, HIGH);
  digitalWrite(PIN_ARMA_ENL, HIGH);
}

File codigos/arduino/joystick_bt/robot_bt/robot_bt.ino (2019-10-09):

#include <SoftwareSerial.h>
SoftwareSerial SerialBT(5, 6); // RX | TX

struct Message {
  int16_t motorSpeedA;
  int16_t motorSpeedB;
  int16_t weaponSpeed;
} message;

struct Motor {
  uint8_t pin;
  int currentSpeed;
  int newSpeed;
  int jumpSpeed;
};

int motorSpeedB = 0;
int motorSpeedA = 0;

int periodo = 100;  //cada cuanto manda datos
unsigned long TiempoAhora = 0;

char char_in1, char_in2;
char *ptr;
struct Message state;
long count;
long sizex;

Motor motorA;
Motor motorB;
Motor weapon;

//bluetooth
#define PIN_BT_TX 5
#define PIN_BT_RX 6

// motor A, izquierdo
#define PIN_MOT_A1 2    //IN1
#define PIN_MOT_A2 4    //IN2
#define PIN_MOT_AEN 3   //ENA

//motor B, derecho
#define PIN_MOT_B1 13    //IN3
#define PIN_MOT_B2 12    //IN4
#define PIN_MOT_BEN 11  //ENB

//motor arma
#define PIN_ARMA_PWMR 10
#define PIN_ARMA_PWML 9
#define PIN_ARMA_ENR 7
#define PIN_ARMA_ENL 8

void setup() {

  configurarMotoresMovimiento();
  configurarArma();
  Serial.begin(9600);
  SerialBT.begin(9600);

  Motor weapon = {PIN_ARMA_PWML, 0, 0,2};
  Motor motorA = {PIN_MOT_AEN, 0, 0,4};
  Motor motorB = {PIN_MOT_BEN, 0, 0,4};
}

void loop() {
  //Recibir mensajes
  leerSerialBT();

  //Para detener todo
  detenertodo();

  // Mover el robot
  setVelMov();

  // Mover el arma
  setVelArma();

  if (millis() >= TiempoAhora + periodo) {
    analogWrite(PIN_ARMA_PWML, weapon.currentSpeed); // Send PWM signal to weapon motor
    analogWrite(PIN_MOT_AEN, motorA.currentSpeed);   // Send PWM signal to motor A
    analogWrite(PIN_MOT_BEN, motorB.currentSpeed);   // Send PWM signal to motor B
  }


}

void setVelArma() {
  weapon.newSpeed = state.weaponSpeed;
  check_vel(&weapon);
}

void check_vel(Motor* motor) {
  if (motor->currentSpeed > motor->newSpeed) {
    motor->currentSpeed -= motor ->jumpSpeed;
  }

  else if (motor->currentSpeed < motor->newSpeed) {
    motor->currentSpeed += motor ->jumpSpeed;
  }
}

void leerSerialBT() {
  SerialBT.listen();
  int rcv_bytes = SerialBT.available();
  //Serial.println("" + String(rcv_bytes));
  if (rcv_bytes == 6) {
    //while (!SerialBT.available());
    sizex = sizeof(struct Message);
    ptr = (char *)&state;
    for (count = 0; count < sizex; count++) {
      *(ptr + count) = SerialBT.read();
    }
  }
}

void setVelMov() {
  motorSpeedA = state.motorSpeedA;
  motorSpeedB = state.motorSpeedB;
  if (state.motorSpeedA < 0) {
    moverRobot_atras();
    motorSpeedA=-1*motorSpeedA;
    motorSpeedB=-1*motorSpeedB;
  }
  else if (state.motorSpeedA > 0) {
    moverRobot_adelante();
  }
  else {
    pararRobot();
  }
  check_vel(&motorA);
  check_vel(&motorB);

}

void detenertodo() {
  if (state.weaponSpeed == -1) {
    pararRobot();
    digitalWrite(PIN_MOT_AEN, LOW);
    digitalWrite(PIN_MOT_BEN, LOW);
    analogWrite(PIN_ARMA_PWML, 0);
    analogWrite(PIN_ARMA_PWMR, 0);
  }
}

void moverRobot_atras() {
  digitalWrite(PIN_MOT_A1, HIGH);
  digitalWrite(PIN_MOT_A2, LOW);
  digitalWrite(PIN_MOT_B1, LOW);
  digitalWrite(PIN_MOT_B2, HIGH);
}

void moverRobot_adelante() {
  digitalWrite(PIN_MOT_A1, LOW);
  digitalWrite(PIN_MOT_A2, HIGH);
  digitalWrite(PIN_MOT_B1, HIGH);
  digitalWrite(PIN_MOT_B2, LOW);
}

void pararRobot() {
  digitalWrite(PIN_MOT_A1, LOW);
  digitalWrite(PIN_MOT_A2, LOW);
  digitalWrite(PIN_MOT_B1, LOW);
  digitalWrite(PIN_MOT_B2, LOW);
}

void configurarBluetooth() {
  pinMode(PIN_BT_TX, INPUT);
  pinMode(PIN_BT_RX, INPUT);
}

void configurarMotoresMovimiento() {
  //Pines Motor A
  pinMode(PIN_MOT_A1, OUTPUT);
  pinMode(PIN_MOT_A2, OUTPUT);
  pinMode(PIN_MOT_AEN, OUTPUT);
  digitalWrite(PIN_MOT_AEN, HIGH);

  //Pines Motor B
  pinMode(PIN_MOT_B1, OUTPUT);
  pinMode(PIN_MOT_B2, OUTPUT);
  pinMode(PIN_MOT_BEN, OUTPUT);
  digitalWrite(PIN_MOT_BEN, HIGH);
}

void configurarArma() {
  //Pines Motor Central
  pinMode(PIN_ARMA_PWMR, OUTPUT);
  pinMode(PIN_ARMA_PWML, OUTPUT);
  pinMode(PIN_ARMA_ENR, OUTPUT);
  pinMode(PIN_ARMA_ENL, OUTPUT);

  digitalWrite(PIN_ARMA_PWMR, LOW);
  digitalWrite(PIN_ARMA_PWML, LOW);
  digitalWrite(PIN_ARMA_ENR, HIGH);
  digitalWrite(PIN_ARMA_ENL, HIGH);
}

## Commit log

2019-06-10 Agregando codigo para controlar por bluetooth
2019-06-10 agregando mas archivos
    [agarre_motorarma.stl, agarre_motorbowl.stl, agarre_yellowmotor1.stl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]
2019-06-12 Incluimos el nombre del robot
2019-06-13 cambio de texto
2019-06-13 Cambiando orden de pines del codigo bluetooth
2019-06-28 Actualizando codigos varios
    [robotito_bluetooth.fzz]
2019-06-28 Correcciones y adicion de contenido
    [robotito_bluetooth.fzz]
2019-07-04 Eliminacion de una linea del README
2019-07-05 Actualizando diagrama
    [robotito_bluetooth.fzz]
2019-07-05 Actualizando README y eliminando esquema anterior
    [robotito_bluetooth.fzz]
2019-07-05 Agregando schematic
2019-07-05 Edicion a schematic
    [robotito_bluetooth.fzz]
2019-07-05 Eliminando archivo
    [robotito_bluetooth.fzz]
2019-07-07 un que
2019-07-07 Elimando esquema en fzz
    [robotito_bluetooth.fzz]
2019-07-07 readme de los planos
2019-07-07 Agregando imagenes de robotito
2019-07-07 readme de diagramas
2019-07-07 cambio de nombre
2019-07-08 Arreglo diagramas
    [robotito_bluetooth.fzz]
2019-07-10 Pequeña modificacion de codigos y correccion de diagramas
2019-08-11 agregando png de la pcb del control
